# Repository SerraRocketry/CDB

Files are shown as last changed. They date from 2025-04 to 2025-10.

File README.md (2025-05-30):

# Aviônica - Computador de Bordo

Este projeto é o computador de bordo (CDB) para o foguete SR1500 da equipe de foguetemodelismo Serra Rocketry. O CDB utiliza sensores e módulos para monitorar a altitude, localização GPS, e controlar a abertura do paraquedas para garantir um voo seguro.

## Funcionalidades

- Leitura de altitude utilizando o sensor BMP280.
- Monitoramento de localização GPS com o módulo GPS NEO-6m.
- Comunicação via LoRa para transmissão de dados com a base operacional.
- Controle de um servo motor para abertura do paraquedas.
- Armazenamento de dados em LittleFS.
- Monitoramento de aceleração e giroscópio utilizando o sensor MPU6050.
- Registro de dados em formato CSV para análise posterior.
- Sinalização com buzzer para indicar status de operação.

## Hardware Utilizado

- ESP32
- Sensor de pressão BMP280
- Módulo GPS NEO-6m
- Módulo LoRa
- Servo motor
- Buzzer
- LED
- Step down
- Baterias 18650
- Sensor MPU6050

## Configuração de Pinos

- **BUZZER_PIN**: 0
- **SERVO_PIN**: 13
- **RX_GPS**: 20
- **TX_GPS**: 21
- **SS_LORA**: 7
- **RST_LORA**: 1
- **DIO0_LORA**: 2

## Bibliotecas Utilizadas

- **Wire**
- **SPI**
- **Adafruit_BMP280**
- **ESP32Servo**
- **TinyGPS++**
- **FS**
- **LittleFS**
- **LoRa**
- **Adafruit_MPU6050**
- **Adafruit_Sensor**

## Estrutura do Código

- **setup()**: Configura os sensores, módulos e inicializa as variáveis.
- **loop()**: Realiza leituras periódicas dos sensores, verifica a altitude e controla a abertura do paraquedas.
- **setupLittleFS()**: Inicializa o sistema de arquivos LittleFS.
- **setupBMP()**: Configura o sensor BMP280.
- **setupLoRa()**: Inicializa o módulo LoRa.
- **setupMPU()**: Configura o sensor MPU6050.
- **setupServo()**: Configura o servo motor.
- **buzzSignal()**: Controla o buzzer para sinalização.
- **logData()**: Registra e imprime os dados do momento.
- **handleParachute()**: Controla a abertura do paraquedas com base na altitude.
- **checkHighest()**: Verifica a maior altitude alcançada.
- **writeFile()**: Escreve dados no arquivo LittleFS.
- **appendFile()**: Anexa dados ao arquivo LittleFS.
- **printBoth()**: Imprime mensagens no Serial e envia via LoRa.
- **sendLoRa()**: Envia mensagens via LoRa.
- **GPSData()**: Obtém dados do GPS (latitude, longitude, satélites, altitude, data e hora).
- **BMPData()**: Obtém dados do sensor BMP280 (altitude e pressão).
- **MPUData()**: Obtém dados do sensor MPU6050 (aceleração e giroscópio).
- **getDataString()**: Concatena os dados do GPS, BMP280, MPU6050 e status do paraquedas em uma string.

## Códigos de Apoio

Os códigos contidos em `/extras` são apoios ao desenvolvimento. Esses códigos são funcionais e testados.
Os códigos contidos em `/test`são apoios ao desenvolvimento, como etapas para construção do código final.

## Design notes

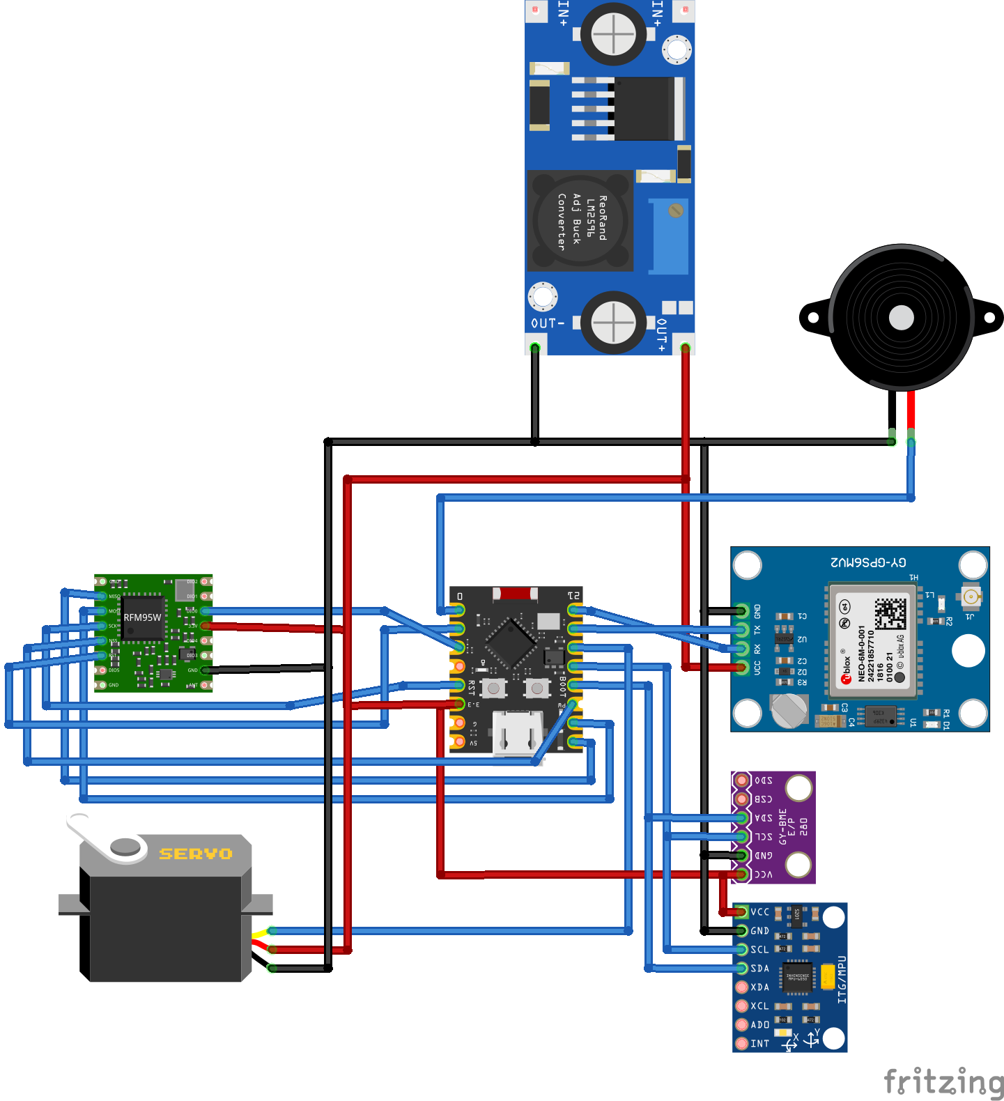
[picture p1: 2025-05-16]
docs/CDB_v2.png

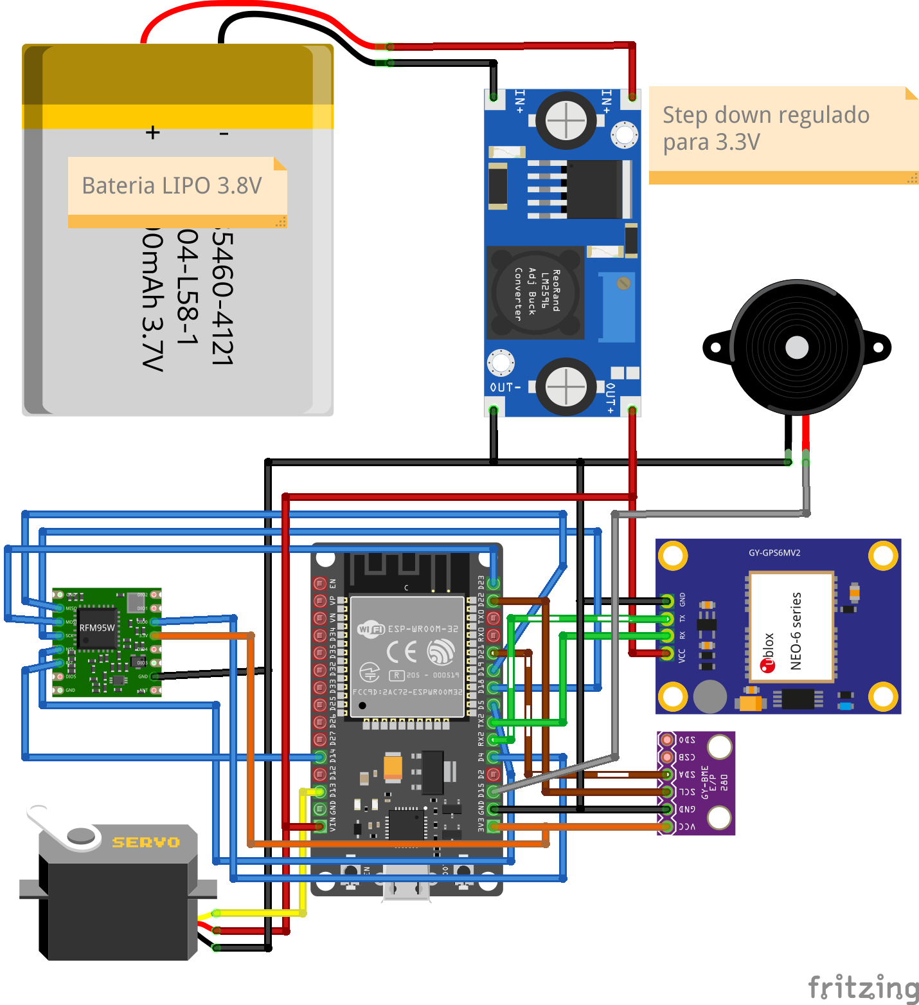
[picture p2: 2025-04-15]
docs/CDB_v1.png

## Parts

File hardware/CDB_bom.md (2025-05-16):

# Bill of Materials: CDB.fzz

| Label | Part Type | Properties |
|---|---|---|
| A2 |Esp32-c3 super mini | variant variant SMD |
| A3 |GY-BMP280 Breakout | variant variant 1 |
| Componente1 |InvenSense MPU6050 | pins 8; variant MPU-6050 |
| J1 |Piezo Speaker | |
| J2 |Basic Servo | |
| M3 |RioRand LM2596 | chip label lm2596; variant variant 2 |
| M4 |NEO-6M GPS Module | model NEO-6M; pins 4; GPS6MV2 |
| RFM95W1 |RFM95W LoRa Module | pins 16; variant 868MHz / 915MHz |

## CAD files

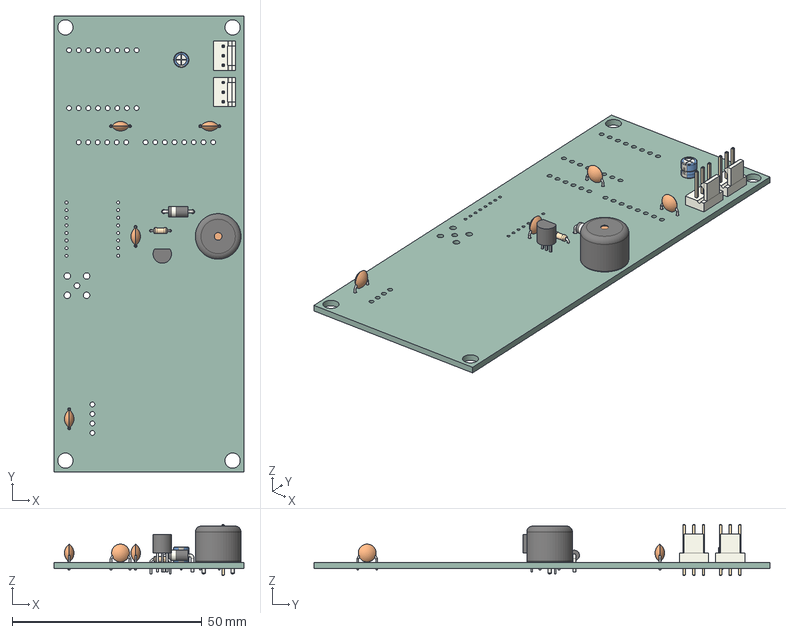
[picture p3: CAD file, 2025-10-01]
hardware/CDB/CDB.step
50.0 x 120.0 x 13.5 mm
D_DO-41_SOD81_P7.62mm_Horizontal
CP_Radial_D40mm_P200mm
C_Disc_D47mm_W25mm_P500mm x 4
Fan_Pin_Header_Straight_1x03 x 2
R_Axial_DIN0204_L36mm_D16mm_P508mm_Horizontal
TO-92_Inline_Narrow
Buzzer_12x95RM76
CDB_PCB

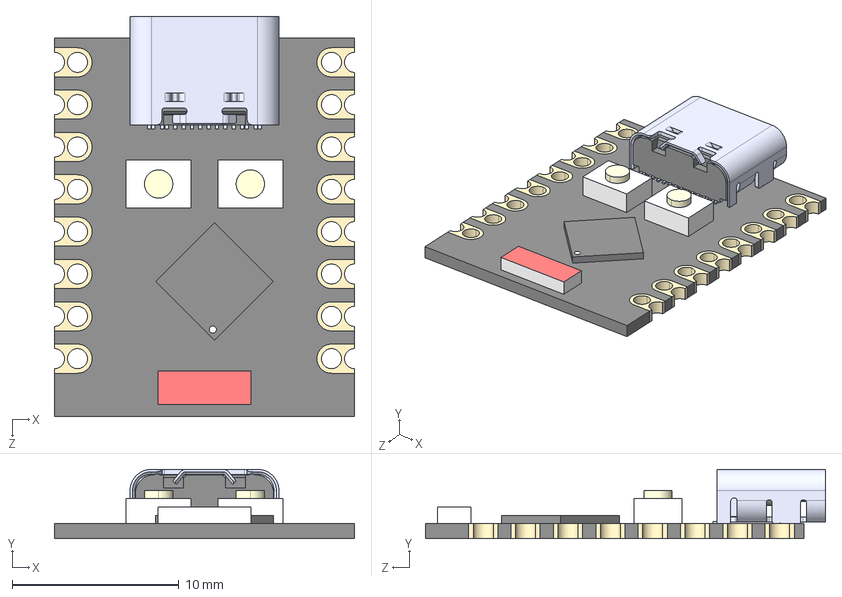
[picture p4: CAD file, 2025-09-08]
hardware/CDB/ESP32-C3_SUPERMINI_TH/ESP32-C3_SUPERMINI_TH.step
18.0 x 4.16 x 24.0 mm
Board c3mini
USB C
components (other)^ESP32-C3 SuperMini

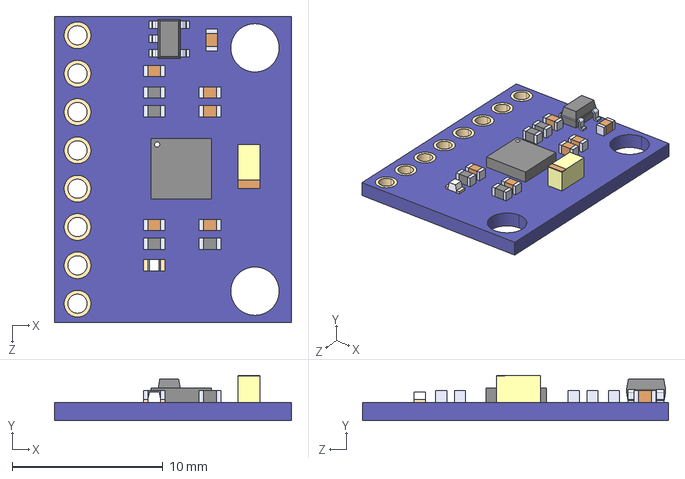
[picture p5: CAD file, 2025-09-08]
hardware/CDB/GY-521/GY-521.step
15.7 x 3.00 x 20.3 mm

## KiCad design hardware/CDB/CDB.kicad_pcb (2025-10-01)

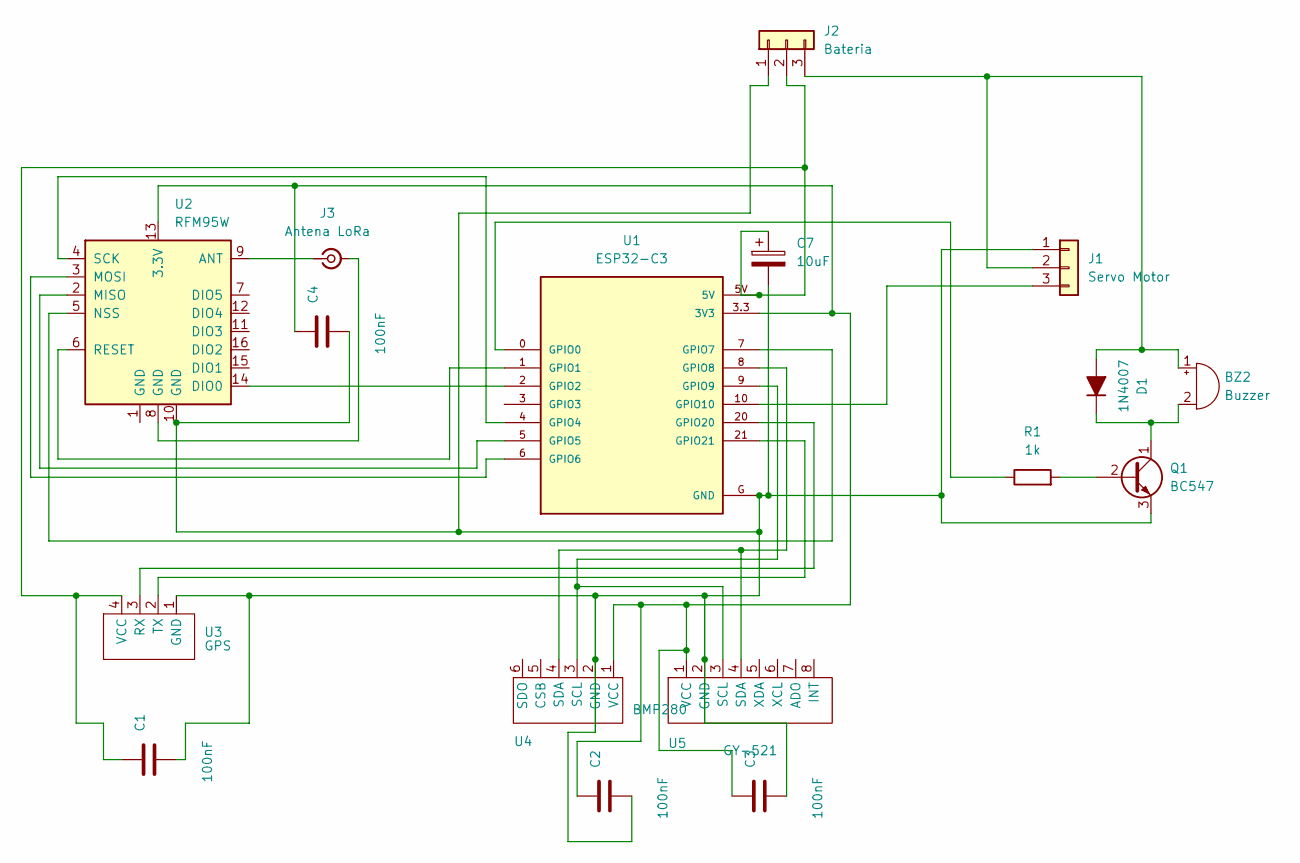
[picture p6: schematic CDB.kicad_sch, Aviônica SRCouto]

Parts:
BZ2: Buzzer; Buzzer_12x9.5RM7.6
C1, C2, C3, C4: 100nF; C_Disc_D4.7mm_W2.5mm_P5.00mm
C7: 10uF; CP_Radial_D4.0mm_P2.00mm
D1: 1N4007; D_DO-41_SOD81_P7.62mm_Horizontal
J1: Servo Motor; FanPinHeader_1x03_P2.54mm_Vertical
J2: Bateria; FanPinHeader_1x03_P2.54mm_Vertical; Part Number 1-0301FBV0T
J3: Antena LoRa; SMA_Amphenol_901-144_Vertical
Q1: BC547; TO-92_Inline
R1: 1k; R_Axial_DIN0204_L3.6mm_D1.6mm_P5.08mm_Horizontal
U1: ESP32-C3; MODULE_ESP32-C3_SUPERMINI
U2: RFM95W; HOPERF_RFM9XW_THT
U3: GPS; GY-NEO6M-V2
U4: BMP280; GY-BMP280
U5: GY-521

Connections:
unnamed: BZ2.1 (+), D1.2 (A), J1.2, J2.3
unnamed: BZ2.2 (-), D1.1 (K), Q1.1 (C)
unnamed: C1.2, C2.2, C3.2, C4.2, C7.2, J1.1, J2.1, Q1.3 (E), U1.G (GND), U2.10 (GND), U3.1 (GND), U4.2 (GND), U5.2 (GND)
unnamed: J1.3, U1.10 (GPIO10)
unnamed: C1.1, C7.1, J2.2, U1.5V, U3.4 (VCC)
unnamed: J3.2 (Ext), U2.8 (GND)
unnamed: J3.1 (In), U2.9 (ANT)
unnamed: Q1.2 (B), R1.2
unnamed: C2.1, C3.1, C4.1, U1.3.3 (3V3), U2.13 (3.3V), U4.1 (VCC), U5.1 (VCC)
unnamed: R1.1, U1.0 (GPIO0)
unnamed: U1.1 (GPIO1), U2.6 (RESET)
unnamed: U1.2 (GPIO2), U2.14 (DIO0)
unnamed: U1.4 (GPIO4), U2.4 (SCK)
unnamed: U1.5 (GPIO5), U2.2 (MISO)
unnamed: U1.6 (GPIO6), U2.3 (MOSI)
unnamed: U1.7 (GPIO7), U2.5 (NSS)
unnamed: U1.8 (GPIO8), U4.4 (SDA), U5.4 (SDA)
unnamed: U1.9 (GPIO9), U4.3 (SCL), U5.3 (SCL)
unnamed: U1.20 (GPIO20), U3.3 (RX)
unnamed: U1.21 (GPIO21), U3.2 (TX)

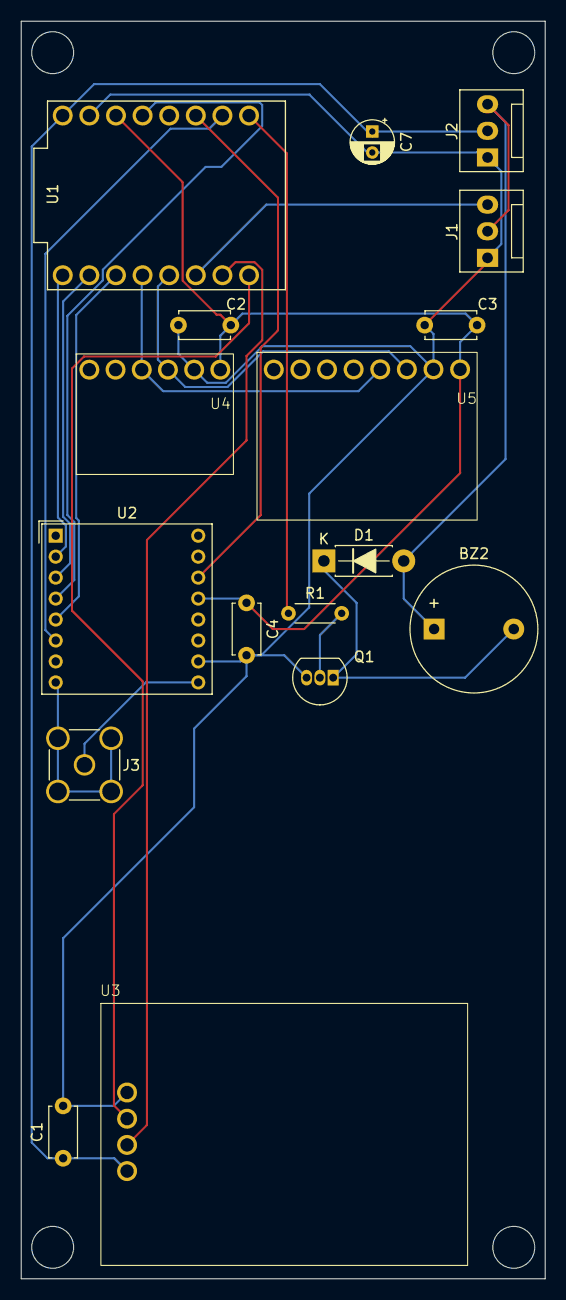
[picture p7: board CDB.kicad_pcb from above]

Board: 2 copper layers, 50.0 x 120.0 mm, 17 parts (0 on the bottom side), 20 nets.

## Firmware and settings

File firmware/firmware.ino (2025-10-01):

// Inclusão de bibliotecas
#include <Wire.h>
#include <SPI.h>
#include <Adafruit_BMP280.h>
#include <ESP32Servo.h>
#include <TinyGPS++.h>
#include "LittleFS.h"
#include <LoRa.h>
#include <Adafruit_MPU6050.h>
#include <Adafruit_Sensor.h>

// Definições de pinos e constantes
#define INTERVAL 200

#define BMP_ADDR 0x76 // Endereço I2C padrão do BMP280

#define LORA_FREQ 868E6 // Frequência de operação
#define SS_LORA 7
#define RST_LORA 1
#define DIO0_LORA 2
#define SYNC_WORD 0xF3 // Código de sincronização

#define SERVO_PIN 10 // Pino do servo motor
#define BUZZER_PIN 0 // Pino do buzzer

#define RX_GPS 20 // RX do GPS
#define TX_GPS 21 // TX do GPS

// Instanciação de objetos
Adafruit_BMP280 BMP;  // Objeto do BMP280
Servo ParachuteServo; // Objeto do servo
TinyGPSPlus GPS;      // Objeto do GPS
Adafruit_MPU6050 MPU; // Objeto do MPU6050

// Variáveis globais
int packet_count = 0; // Contador de pacotes
unsigned long previous_millis = 0;
float previous_altitude = 0, max_altitude = 0, base_altitude = 0; // Altitudes variáveis e estáticas
float base_pressure = 0;                                          // Pressão na base
String file_name = "Dados.csv";                                   // Nome do arquivo para salvar os dados
String file_dir = "";                                             // Diretório do arquivo
String state = "";                                                // Estado do sistema
bool parachute_deployed = false;                                  // Verificação da liberação do paraquedas
const int MAXPOS = 180, MINPOS = 0;                               // Posição máxima e mínima do servo
const float ALTITUDE_DROP_THRESHOLD = 10.0;                       // Ao menos 10m abaixo do referencial máximo (ajustar se necessário)
const float ALTITUDE_THRESHOLD = 200.0;                           // Altura mínima para liberar o paraquedas (ajustar se necessário)
const float VELOCITY_THRESHOLD = 5.0;                             // Velocidade de descida mínima para liberar o paraquedas (ajustar se necessário)
const String TEAM_ID = "100";                                     // ID da equipe
sensors_event_t acc, gyr, temp;                                   // Variáveis para armazenar os dados do MPU6050

// Setup da memória LittleFS
bool setupLittleFS()
{
  if (!LittleFS.begin(true))
  {
    Serial.println("Erro ao montar LittleFS.");
    return false;
  }
  return true; // Retorna true se tudo ocorreu bem
}

// Setup do módulo BMP280
bool setupBMP()
{
  if (!BMP.begin(BMP_ADDR))
  {
    Serial.println("Falha no BMP280.");
    return false;
  }
  base_pressure = BMP.readPressure() / 100;
  previous_altitude = BMP.readAltitude(base_pressure);
  max_altitude = previous_altitude;
  base_altitude = previous_altitude;
  return true; // Retorna true se tudo ocorreu bem
}

// Setup do módulo LoRa
bool setupLoRa()
{
  LoRa.setPins(SS_LORA, RST_LORA, DIO0_LORA);
  if (!LoRa.begin(LORA_FREQ))
  {
    Serial.println("Falha ao inicializar o LoRa.");
    return false;
  }
  LoRa.setSyncWord(SYNC_WORD);
  return true; // Retorna true se tudo ocorreu bem
}

// Setup do MPU6050
bool setupMPU()
{
  if (!MPU.begin())
  {
    Serial.println("Falha no MPU6050.");
    return false;
  }
  return true; // Retorna true se tudo ocorreu bem
}

// Setup do servo motor
void setupServo()
{
  ParachuteServo.attach(SERVO_PIN);
  ParachuteServo.write(MINPOS);
}

// Sinalização com o buzzer
void buzzSignal(String signal)
{
  int frequency = 1000;   // Frequência do tom
  if (signal == "Alerta") // Alerta de erro em alguma configuração
  {
    for (int i = 0; i < 5; i++)
    {
      tone(BUZZER_PIN, frequency, 200);
      delay(200 + 150);
    }
  }
  else if (signal == "Sucesso") // Sinal de sucesso na configuração
  {
    for (int i = 0; i < 3; i++)
    {
      tone(BUZZER_PIN, frequency, 100);
      delay(100 + 100);
    }
  }
  else if (signal == "Ativado")
  {
    tone(BUZZER_PIN, frequency, 500);
  }
  else if (signal == "Beep") // Beep de funcionamento padrão
  {
    tone(BUZZER_PIN, frequency, 50);
  }
  else
  {
    Serial.println("Sinal inválido!");
  }
}

// Registra e imprime os dados do momento
// Formato: TEAM_ID,millis,count,hora,data,alt,lat,lon,sat,altp,temp,p,gp,gr,gy,ap,ar,ay
void logData(unsigned long current_millis)
{
  String readings = getDataString();                                                                                 // Obtém os dados do GPS, BMP280 e MPU6050
  String data_string = TEAM_ID + String(current_millis) + "," + String(packet_count) + "," + state + "," + readings; // String com os dados atuais
  printBoth(data_string);
  appendFile(file_dir, data_string);
  packet_count++;
}

// Verifica se a altura atual é a máxima já atingida
void checkHighest(float altitude)
{
  if (altitude > max_altitude)
  {
    max_altitude = altitude;
  }
}

// Lida com a abertura do paraquedas
void handleParachute(float altitude, float velocity)
{
  if (!parachute_deployed) // Confere se o paraquedas já foi acionado
  {
    if (altitude <= max_altitude - ALTITUDE_DROP_THRESHOLD && (altitude < ALTITUDE_THRESHOLD || abs(velocity) > VELOCITY_THRESHOLD)) // Se a altitude cair 10m abaixo do referencial máximo e for menor que 100m
    {
      ParachuteServo.write(MAXPOS);
      unsigned long startTime = millis();
      while (millis() - startTime < 500) // Aguarda 500ms para conferir se o servo motor abriu
      {
        if (ParachuteServo.read() == MAXPOS)
        {
          break;
        }
      }
      if (ParachuteServo.read() != MAXPOS)
      {
        printBoth("ERRO: Servo não abriu!");
      }
      printBoth("Paraquedas acionado. Altitude: " + String(altitude));
      parachute_deployed = true;
    }
  }
  else
  {
    buzzSignal("Ativado");
  }
  previous_altitude = altitude;
}

// Escreve os dados no arquivo - escrita
bool writeFile(const String &path, const String &data_string)
{
  File file = LittleFS.open(path, FILE_WRITE);
  if (!file) // Se houver falha ao abrir o arquivo
  {
    Serial.println("Falha ao abrir arquivo para gravação.");
    return false;
  }
  if (file.println(data_string)) // Se a escrita no arquivo for bem-sucedida
  {
    Serial.println("Arquivo escrito.");
  }
  else // Se houver falha na escrita
  {
    Serial.println("Falha na gravação do arquivo.");
    file.close();
    return false;
  }
  file.close();
  return true; // Retorna true se tudo ocorreu bem
}

// Escreve os dados no arquivo - anexação
void appendFile(const String &path, const String &message)
{
  File file = LittleFS.open(path, FILE_APPEND);
  if (!file) // Se houver falha ao abrir o arquivo
  {
    Serial.println("Falha ao abrir arquivo para anexar.");
  }
  if (file.print(message + "\n")) // Se a escrita no arquivo for bem-sucedida
  {
    Serial.println("Mensagem anexada.");
  }
  else // Se houver falha na escrita
  {
    Serial.println("Falha ao anexar mensagem.");
    file.close();
  }
  file.close();
}

// Imprime a mensagem no Serial e no LoRa
void printBoth(const String &message)
{
  Serial.println(message);
  sendLoRa(message);
}

// Processa o envio de mensagens LoRa
void sendLoRa(const String &message)
{
  LoRa.beginPacket();
  LoRa.print(message);
  if (LoRa.endPacket())
  {
    Serial.println("Mensagem LoRa enviada.");
  }
  else
  {
    Serial.println("ERRO ao enviar mensagem LoRa!");
  }
  LoRa.endPacket();
}

// Retorna os dados de hora, data, altitude, latitude, longitude, satélites
String GPSData()
{
  while (Serial1.available() > 0)
  {
    GPS.encode(Serial1.read());
  }

  String date_data = "N/A"; // String da data
  if (GPS.date.isValid())
  {
    date_data = "," + String(GPS.date.year()) + "/" +
                String(GPS.date.month()) + "/" +
                String(GPS.date.day());
  }

  String time_data = ",N/A"; // String do horário
  if (GPS.time.isValid())
  {
    time_data = "," + String(GPS.time.hour()) + ":" +
                String(GPS.time.minute()) + ":" +
                String(GPS.time.second());
  }

  String location_data = ",N/A,N/A,N/A,N/A,N/A"; // String da localização lat-long-satélites-altitude
  if (GPS.location.isValid())
  {
    location_data = String(GPS.altitude.meters()) + "," +
                    String(GPS.location.lat(), 8) + "," +
                    String(GPS.location.lng(), 8) + "," +
                    String(GPS.satellites.value());
  }

  return time_data + date_data + location_data;
}

// Retorna os dados de altitude, temperatura, pressão
String BMPData()
{
  return String(BMP.readAltitude(base_pressure)) + "," +
         String(BMP.readTemperature()) + "," +
         String(BMP.readPressure() / 100.0F);
}

// Retorna os dados de giroscópio, acelerômetro
String MPUData()
{
  MPU.getEvent(&acc, &gyr, &temp); // Lê os dados do MPU6050

  float ap = acc.acceleration.x; // Aceleração em x - pitch
  float ar = acc.acceleration.y; // Aceleração em y - roll
  float ay = acc.acceleration.z; // Aceleração em z - yaw

  float gp = gyr.gyro.x; // Giroscópio em x - pitch
  float gr = gyr.gyro.y; // Giroscópio em y - roll
  float gy = gyr.gyro.z; // Giroscópio em z - yaw

  return String(gp) + "," +
         String(gr) + "," +
         String(gy) + "," +
         String(ap) + "," +
         String(ar) + "," +
         String(ay);
}

// Retorna a string com os dados do BMP280, MPU6050 e GPS
String getDataString()
{
  return BMPData() + "," + MPUData() + "," + GPSData();
}

void setup()
{
  Serial.begin(115200);
  setupServo(); // Inicia o servo motor

  pinMode(BUZZER_PIN, OUTPUT);
  for (int i = 0; i < 5; i++)
  {
    Serial.println("Inicializando...");
    delay(1000);
  }

  Serial1.begin(9600, SERIAL_8N1, RX_GPS, TX_GPS); // Inicia o GPS (precisa ser o Serial1)
  if (!Serial1)
  {
    Serial.println("Falha ao iniciar o GPS.");
    delay(3000);
    ESP.restart();
  }
  delay(1000); // Aguarda o GPS inicializar

  while (true)
  {
    while (Serial1.available() > 0)
    {
      GPS.encode(Serial1.read());
    }
    Serial.println("Aguardando GPS...");
    if (GPS.location.isValid())
    {
      break;
    }
    delay(500);
  }

  String time_data = ""; // String do horário
  time_data = String(GPS.time.hour()) + ":" +
              String(GPS.time.minute()) + ":" +
              String(GPS.time.second());

  file_dir = "/" + time_data + "-" + file_name; // Diretório do arquivo de dados
  Serial.print("Salvando dados em: ");
  Serial.println(file_dir);
  String data_header = "TEAM_ID,millis,count,hora,data,alt,lat,lon,sat,altp,temp,p,gp,gr,gy,ap,ar,ay"; // Cabeçalho do arquivo
  if (!(setupLittleFS() && writeFile(file_dir, data_header)))                                          // Inicia a memória interna
  {
    Serial.println("Erro no sistema de arquivos!");
    buzzSignal("Alerta");
    delay(3000);
    ESP.restart();
  }

  if (!(setupBMP() && setupMPU() && setupLoRa())) // Inicia os módulos BMP, MPU6050 e LoRa
  {
    Serial.println("Erro na configuração dos módulos!");
    buzzSignal("Alerta");
    delay(3000);
    ESP.restart();
  }

  buzzSignal("Sucesso");
}

void loop()
{
  unsigned long current_millis = millis();
  if (current_millis - previous_millis >= INTERVAL) // A cada 200ms
  {
    logData(current_millis);
    float altitude = BMP.readAltitude(base_pressure);
    float velocity = (altitude - previous_altitude) / ((current_millis - previous_millis) / 1000.0); 
    checkHighest(altitude);
    handleParachute(altitude, velocity);
    previous_millis = current_millis;
  }
}

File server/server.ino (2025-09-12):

#include <ArduinoJson.h>
#include <ESPAsyncWebServer.h>
#include <LittleFS.h>
#include <WiFi.h>

// Credenciais de acesso à rede.
const char *ssid = "Servidor ESP32";
const char *password = "12345678";

// Instancia um servidor http que escutará na porta 80.
AsyncWebServer server(80);

void setServerRoutes() {
  // Rotas básicas de acesso ao site para o usuário
  server.on("/", HTTP_GET, [](AsyncWebServerRequest* request) {
    request->send(LittleFS, "/index.html", "text/html");
  });

  server.on("/style.css", HTTP_GET, [](AsyncWebServerRequest* request) {
    request->send(LittleFS, "/style.css", "text/css");
  });

  server.on("/index.js", HTTP_GET, [](AsyncWebServerRequest* request) {
    request->send(LittleFS, "/index.js", "application/javascript");
  });

  // Rotas API que permitem que o front-end tenha acesso aos dados do back-end.
  // Não é exatamente RESTful por limitações de capacidades da lib, de recursos
  // do ESP32 e de minha própria habilidade lol.

  // Essa rota captura todos os arquivos dispostos na raiz do Sistema de
  // Arquivos e retorna alguns de seus dados. É usado na homepage para popular a
  // tabela.
  server.on("/api/files", HTTP_GET, [](AsyncWebServerRequest* request) {
    JsonDocument fsFiles; // Cria um objeto JSON.
    File root = LittleFS.open("/"); // Abre o Sistema de Arquivos na Raiz.

    // Para todos os arquivos nesse diretório:
    File file = root.openNextFile();
    while (file) {
      if (!file.isDirectory()) {
        // Adicione seu nome e tamanho no objeto JSON.
        JsonObject fsFile = fsFiles.add<JsonObject>();
        fsFile["name"] = String(file.name());
        fsFile["size"] = file.size();
      }
      file = root.openNextFile();
    }
    // Por fim, transforme o objeto JSON em sua representação texto puro e o
    // envie para o cliente.
    char jsonString[8000] = { 0 };
    serializeJson(fsFiles, jsonString);
    request->send(200, "application/json; charset=utf-8", jsonString);
  });

  // Essa rota captura um arquivo específico na raiz do Sistema de Arquivos e o
  // retorna para o cliente. Consumida pelo front-end quando os links de abrir e
  // baixar arquivos são selecionados.
  server.on("/api/file", HTTP_GET, [](AsyncWebServerRequest* request) {
    // Só retormamos com sucesso se o cliente requisitou um arquivo.
    if (!(request->hasParam("filename"))) {
      request->send(400, "text/plain; charset=utf-8", "Parâmetro de URL \
          <filename> faltando.");
      return;
    }

    // Só retormamos com sucesso se arquivo requisitado existe no Sistema de
    // Arquivos.
    const AsyncWebParameter* param = request->getParam("filename");
    String filename = param->value();
    if (!LittleFS.exists("/" + filename)) {
      request->send(404, "text/plain; charset=utf-8", "Arquivo <" + filename + 
          "> não encontrado no Sistema de Arquivos");
      return;
    }

    // Retornamos o arquivo para download ou visualização simples dependendo se
    // o cliente enviou também o parâmetro de URL <download>. (Deve ter uma
    // solução mais elegante pra isso).
    if (request->hasParam("download")) {
      request->send(LittleFS, "/" + filename, String(), true);
    } else {
      request->send(LittleFS, "/" + filename, "text/plain; charset=utf-8");
    }
  });

  // Muito semelhante a rota anterior, só que agora que verbo HTTP mudou de GET
  // para DELETE nós deletamos o arquivo no Sistema de Arquivos ao invés de
  // retorná-lo pro cliente. Consumida pelo front-end quando o cliente seleciona
  // o botão de deletar arquivos.
  server.on("/api/file", HTTP_DELETE, [](AsyncWebServerRequest* request) {
    Serial.println(request->method());
    if (!(request->hasParam("filename"))) {
      request->send(400, "text/plain; charset=utf-8", "Parâmetro de URL \
          <filename> faltando.");
      return;
    }

    const AsyncWebParameter* param = request->getParam("filename");
    String filename = param->value();

    if (!LittleFS.exists("/" + filename)) {
      request->send(404, "text/plain; charset=utf-8", "Erro ao tentar deletar \
          arquivo <" + filename + "> inexistente.");
      return;
    }

    if (LittleFS.remove("/" + filename)) {
      request->send(200, "text/plain; charset=utf-8", "Arquivo deletado com \
          sucesso.");
    } else {
      // A essa altura nada deve dar de errado, mas por via das dúvidas...
      request->send(400, "text/plain; charset=utf-8", "Erro desconhecido ao \
          tentar deletar arquivo <" + filename + ">");
    }
  });
}

void setup() {
  // Inicializa comunicação serial.
  Serial.begin(115200);

  // Inicializa do Sistema de Arquivos Interno.
  if (!LittleFS.begin()) {
    Serial.println("Um erro ocorreu ao montar LittleFS");
    return;
  }

  // Cria ponto de acesso wireless.
  WiFi.softAP(ssid, password);
  Serial.println("Criando ponto de acesso WiFi..");
  Serial.println(WiFi.softAPIP());

  // Configura as rotas do servidor e o inicializa.
  setServerRoutes();
  server.begin();
}

void loop() {
}

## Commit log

2025-03-04 Update geral
    [Untitled Sketch 2.fzz]
2025-04-15 RM SIM800L
    [CDB.csv, CDB.fzz, Untitled Sketch 2.fzz]
2025-04-15 Update estrutura geral
    [CDB.csv, CDB.fzz]
2025-05-11 add mpu6050
    [CDB.fzz]
2025-05-11 rename all
    [CDB.csv, CDB.fzz]
2025-05-16 update little fs, File browser, open data, BOM
    [12_6_8-Dados.csv, CDB.csv, CDB.fzz]
2025-05-30 update buzzer
    [12_6_8-Dados.csv, log.csv]
2025-09-08 update na string de dados e no envio lora
    [13_30_11-Dados.csv, CDB.kicad_pcb, CDB.kicad_sch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]
2025-09-12 Adição de um sketch com servidor http novo (#1)
    * Feat: Adiciona arquivo inicial
    Esse sketch conterá código similar ao que está disponível no
    FileBrowser.ino, um servidor http para acesso facilitado aos sistema de
    arquivos internos do ESP32, contudo com o front-end e o back-end
    desacoplados.
    * Feat: Adiciona Acess Point LAN ao ESP32
    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
2025-10-01 add velocity threshold
    [CDB.kicad_pcb, CDB.kicad_sch, CDB.step]
